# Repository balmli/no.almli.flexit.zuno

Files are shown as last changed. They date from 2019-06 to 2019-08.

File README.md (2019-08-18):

# Flexit SP 30

Flexit SP 30 panel to Z-UNO.

### Hardware

- [Z-UNO](https://products.z-wavealliance.org/products/1825)
- [SP425 controller board](https://www.flexit.no/produkter/ventilasjonsaggregat/utgatte_modeller/tilbehor_aggregater_utgatte_modeller/sp425_styringskort_for_sentralstyring_sd/styringskort_data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)
- 3 x 3 V relays
- 3 x 817 optocouplers
- 4 x DS18B20 temperature sensors 
- RJ45 wire
- breadboard
- resistors
- wires

### Build instructions:

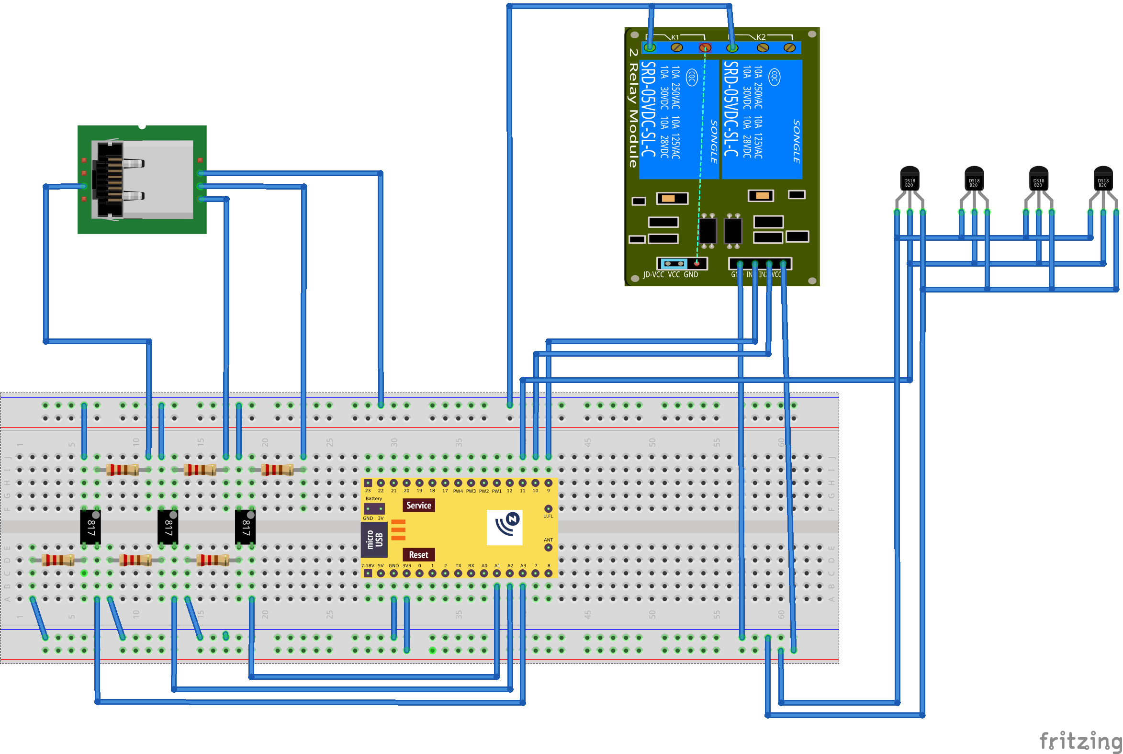
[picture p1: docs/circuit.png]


Connect the three 3 V relays to the Z-UNO:
- Z-UNO, pin  9: to relay 1 in
- Z-UNO, pin 10: to relay 2 in
- Z-UNO, pin 11: to relay 3 in
- 3V to relay Vin
- GND to relay GND-in

Connect the fan RJ45 wire to the breadboard:
- wire pin 3: to a diode, and then to relay 3 out
- wire pin 3: with a 1 kΩ resistor to optocoupler 3 input 
- wire pin 4: to relay 1,2,3 GND-out
- wire pin 5: to a 2.2 kΩ resistor, and then to relay 1 out
- wire pin 5: with a 1 kΩ resistor to optocoupler 1 input 
- wire pin 6: to a 2.2 kΩ resistor, and then to relay 2 out
- wire pin 6: with a 1 kΩ resistor to optocoupler 2 input 
- wire pin 7: to optocoupler 1,2,3 GND-in 

Connect the three optocouplers to the Z-UNO:
- optocoupler 1 out: to Z-UNO, pin A1
- optocoupler 2 out: to Z-UNO, pin A2
- optocoupler 3 out: to Z-UNO, pin A3
- optocoupler 1,2,3 GND-out: with 1 kΩ resistors to GND

Connect the four DS18B20 temperature sensors to the Z-UNO:
- Z-UNO, pin 12: to DS18B20 data pin
- 4.7 kΩ pullup resistor for DS18B20 data pin
- 5V to DS18B20 5V pins
- GND to DS18B20 GND pins

Connect power to the Z-UNO:
- Z-UNO, USB: power source
- Z-UNO, GND

### Firmware

Upload to Z-UNO by:

- install the Z-UNO software version 2.1.5 for Arduino.  See '[here](https://z-uno.z-wave.me/install)' for instructions.
- upload '[firmware](https://github.com/balmli/no.almli.flexit.zuno/blob/master/Flexit_SP30_ZUNO/Flexit_SP30_ZUNO.ino)'.

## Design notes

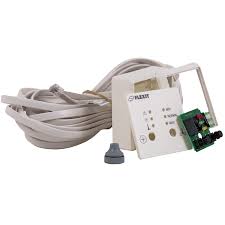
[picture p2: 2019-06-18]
docs/sp30.jpeg

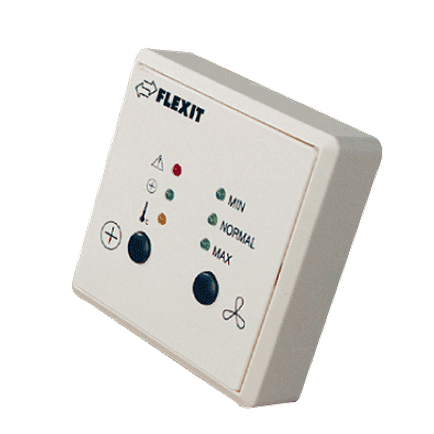
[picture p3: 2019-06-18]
docs/sp30.png

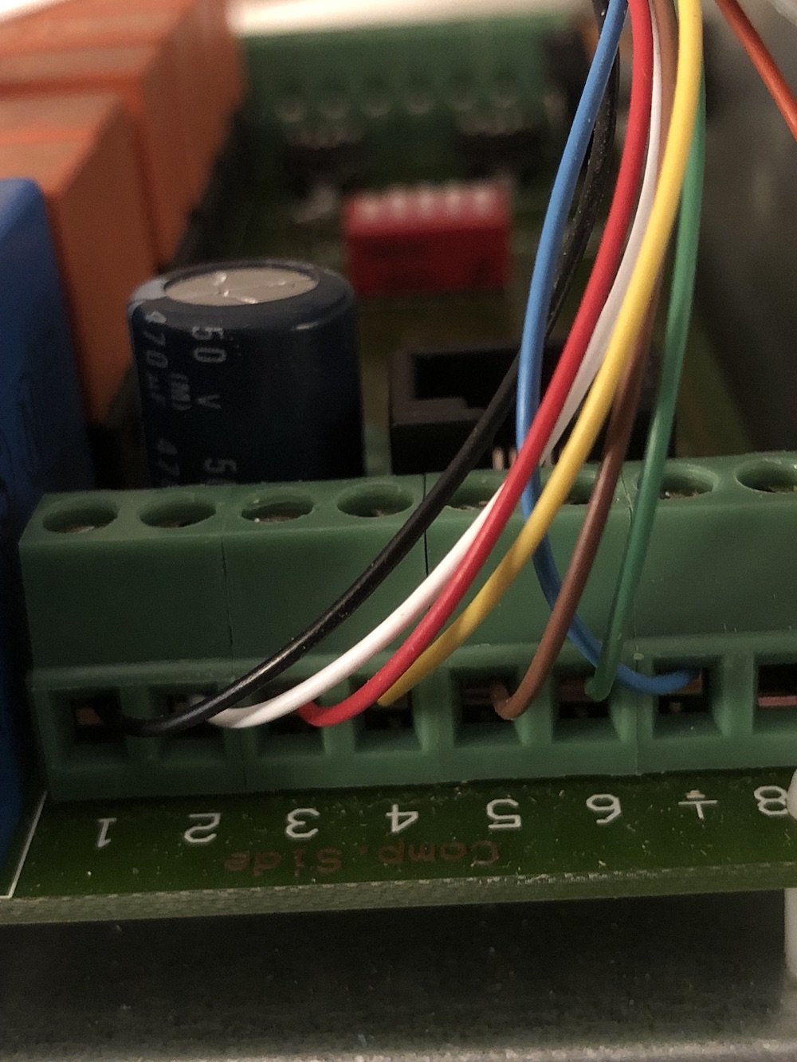
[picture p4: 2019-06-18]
docs/pins.jpg

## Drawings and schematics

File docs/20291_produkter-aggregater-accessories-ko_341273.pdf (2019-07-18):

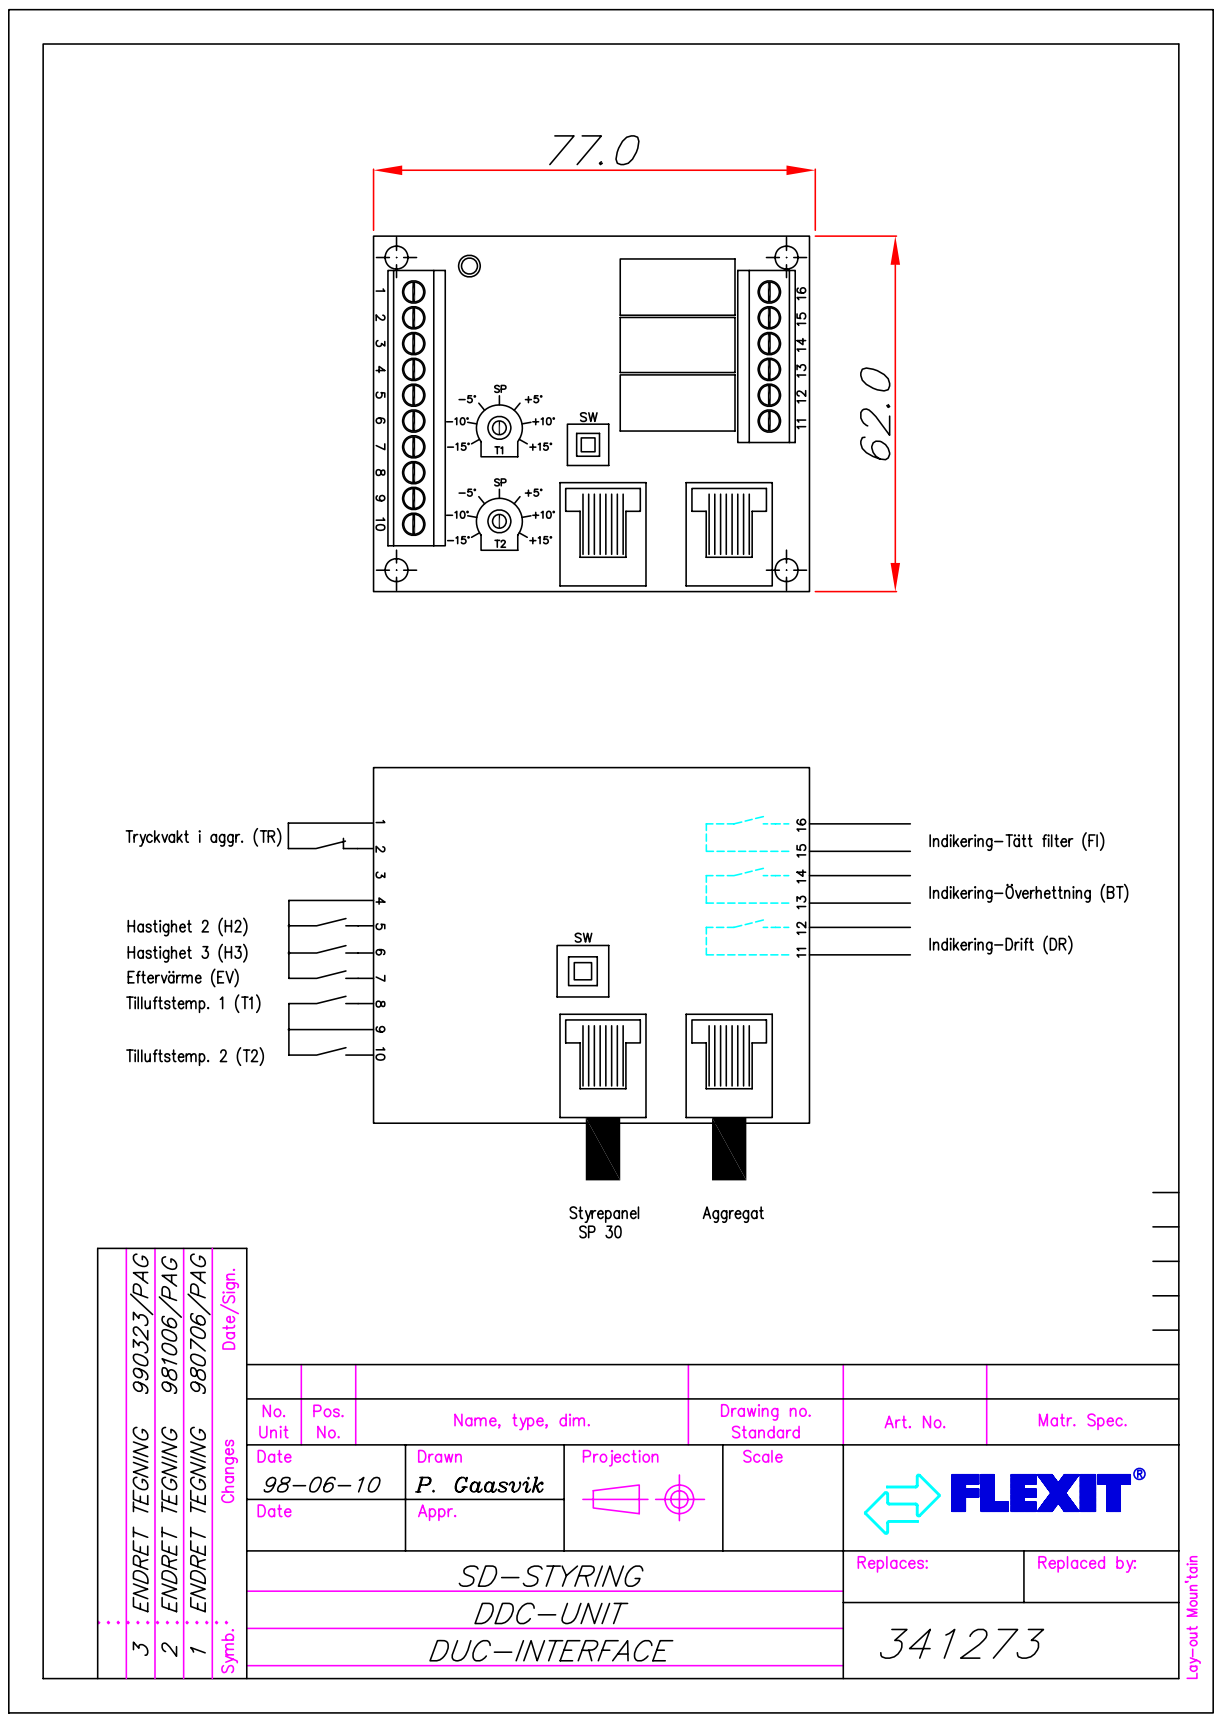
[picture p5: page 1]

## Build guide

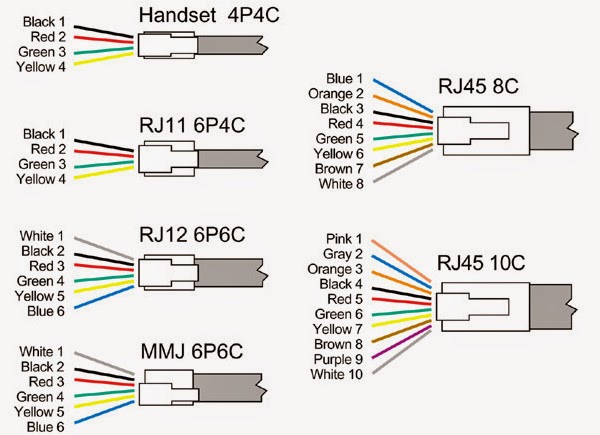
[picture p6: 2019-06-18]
docs/wiring_ms_modular_colour_codes_lg.jpg

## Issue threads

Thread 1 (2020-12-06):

Esphome variation

TomTorger, 2020-12-06:
Great work! Really helps me figuring this out :-)

I am considering doing this for with an esp32 and espHome for home assistant.

I am a bit in doubt as to the function of the relays... I am figuring they are similar to the "push-bottoms"? However, there are two/three 10 A relays in parallel according to your diagram? Could we use optocouplers here as well? (not a pro :-) )

Do you have a description of the pins 1-8 on the SP30 board? And does it supply a DC voltage above 5V somewhere?

Tom

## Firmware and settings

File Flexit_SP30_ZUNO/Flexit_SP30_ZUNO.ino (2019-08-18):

#include "ZUNO_DS18B20.h"
#include "EEPROM.h"

#define DEBUG_x

#define RELAY_1_PIN                 9
#define RELAY_2_PIN                 10
#define RELAY_3_PIN                 11
#define DS18B20_BUS_PIN             12
#define FAN_LEVEL_1_PIN             A1
#define FAN_LEVEL_2_PIN             A2
#define HEATING_PIN                 A3
#define LED_PIN                     LED_BUILTIN

#define MIN_UPDATE_DURATION         30000
#define MIN_STATE_UPDATE_DURATION   1000
#define MIN_TEMP_UPDATE_DURATION    30000
#define LED_BLINK_DURATION          25

OneWire ow(DS18B20_BUS_PIN);
DS18B20Sensor ds18b20(&ow);

#define MAX_TEMP_SENSORS            4
#define ADDR_SIZE                   8
byte addresses[ADDR_SIZE * MAX_TEMP_SENSORS];
#define ADDR(i) (&addresses[i * ADDR_SIZE])
byte temp_sensors;
word temperature[MAX_TEMP_SENSORS];
word temperatureReported[MAX_TEMP_SENSORS];
word temperatureCalibration[MAX_TEMP_SENSORS];

byte mode = 1;
byte modeChanged = 0;
unsigned long lastSetMode = 0;
byte lastFanLevel = 1;
byte lastFanLevelReported = 99;
byte lastHeating = 0;
byte lastHeatingReported = 99;

unsigned long relayTimer = 0;
unsigned long fanLevelTimer = 0;
unsigned long fanLevelTimer2 = 0;
unsigned long heatingTimer = 0;
unsigned long heatingTimer2 = 0;
unsigned long temperatureTimer[MAX_TEMP_SENSORS];
unsigned long ledTimer = 0;
unsigned long listConfigTimer = 0;

word status_report_interval_config;
word temperature_report_interval_config;
word temperature_report_threshold_config;
word relay_duration_config;
word enabled_config;
word enabled_mode_config;
word default_config_set_config;

ZUNO_SETUP_SLEEPING_MODE(ZUNO_SLEEPING_MODE_ALWAYS_AWAKE);
ZUNO_SETUP_PRODUCT_ID(0xC0, 0xC0);
ZUNO_SETUP_CFGPARAMETER_HANDLER(config_parameter_changed);

ZUNO_SETUP_CHANNELS(
    ZUNO_SWITCH_MULTILEVEL(getterMode, setterMode),

    ZUNO_SENSOR_MULTILEVEL(ZUNO_SENSOR_MULTILEVEL_TYPE_GENERAL_PURPOSE_VALUE,
        SENSOR_MULTILEVEL_SCALE_PERCENTAGE_VALUE,
        SENSOR_MULTILEVEL_SIZE_ONE_BYTE,
        SENSOR_MULTILEVEL_PRECISION_ZERO_DECIMALS,
        getterFanLevel),

    ZUNO_SENSOR_MULTILEVEL(ZUNO_SENSOR_MULTILEVEL_TYPE_GENERAL_PURPOSE_VALUE,
        SENSOR_MULTILEVEL_SCALE_PERCENTAGE_VALUE,
        SENSOR_MULTILEVEL_SIZE_ONE_BYTE,
        SENSOR_MULTILEVEL_PRECISION_ZERO_DECIMALS,
        getterHeating),

    ZUNO_SENSOR_MULTILEVEL(ZUNO_SENSOR_MULTILEVEL_TYPE_TEMPERATURE,
        SENSOR_MULTILEVEL_SCALE_CELSIUS,
        SENSOR_MULTILEVEL_SIZE_TWO_BYTES,
        SENSOR_MULTILEVEL_PRECISION_TWO_DECIMALS,
        getterTemp1),

    ZUNO_SENSOR_MULTILEVEL(ZUNO_SENSOR_MULTILEVEL_TYPE_TEMPERATURE,
        SENSOR_MULTILEVEL_SCALE_CELSIUS,
        SENSOR_MULTILEVEL_SIZE_TWO_BYTES,
        SENSOR_MULTILEVEL_PRECISION_TWO_DECIMALS,
        getterTemp2),

    ZUNO_SENSOR_MULTILEVEL(ZUNO_SENSOR_MULTILEVEL_TYPE_TEMPERATURE,
        SENSOR_MULTILEVEL_SCALE_CELSIUS,
        SENSOR_MULTILEVEL_SIZE_TWO_BYTES,
        SENSOR_MULTILEVEL_PRECISION_TWO_DECIMALS,
        getterTemp3),

    ZUNO_SENSOR_MULTILEVEL(ZUNO_SENSOR_MULTILEVEL_TYPE_TEMPERATURE,
        SENSOR_MULTILEVEL_SCALE_CELSIUS,
        SENSOR_MULTILEVEL_SIZE_TWO_BYTES,
        SENSOR_MULTILEVEL_PRECISION_TWO_DECIMALS,
        getterTemp4)
);

void setterMode(byte value) {
    mode = value;
    modeChanged = 1;
    lastSetMode = millis();
}

byte getterMode(void) {
    return mode;
}

byte getterFanLevel(void) {
  return lastFanLevel;
}

byte getterHeating(void) {
  return lastHeating;
}

word getterTemp1() {
    return temperature[0];
}

word getterTemp2() {
    return temperature[1];
}

word getterTemp3() {
    return temperature[2];
}

word getterTemp4() {
    return temperature[3];
}

void config_parameter_changed(byte param, word value) {
    if (param == 64) {
        status_report_interval_config = value;
    }
    if (param == 65) {
        temperature_report_interval_config = value;
    }
    if (param == 66) {
        temperature_report_threshold_config = value;
    }
    if (param == 67) {
        relay_duration_config = value;
    }
    if (param == 68) {
        enabled_config = value;
        if (enabled_config < 0 || enabled_config > 1) {
            enabled_config = 0;
        }
    }
    if (param == 69) {
        enabled_mode_config = value;
        if (enabled_mode_config < 0 || enabled_mode_config > 1) {
            enabled_mode_config = 0;
        }
    }
    if (param >= 70 && param <= 73) {
        temperatureCalibration[param - 70] = value;
    }

#ifdef DEBUG
    Serial.print("config ");
    Serial.print(param);
    Serial.print(" = ");
    Serial.println(value);
#endif
}

void setup() {
    pinMode(RELAY_1_PIN, OUTPUT);
    pinMode(RELAY_2_PIN, OUTPUT);
    pinMode(RELAY_3_PIN, OUTPUT);
    digitalWrite(RELAY_1_PIN, HIGH);
    digitalWrite(RELAY_2_PIN, HIGH);
    digitalWrite(RELAY_3_PIN, HIGH);
    pinMode(LED_PIN, OUTPUT);

    pinMode(FAN_LEVEL_1_PIN, INPUT_PULLUP);
    pinMode(FAN_LEVEL_2_PIN, INPUT_PULLUP);
    pinMode(HEATING_PIN, INPUT_PULLUP);

    Serial.begin();
    fetchConfig();
    temp_sensors = ds18b20.findAllSensors(addresses);
    fetchMode();
}

void fetchConfig() {
    status_report_interval_config = zunoLoadCFGParam(64);
    temperature_report_interval_config = zunoLoadCFGParam(65);
    temperature_report_threshold_config = zunoLoadCFGParam(66);
    relay_duration_config = zunoLoadCFGParam(67);
    enabled_config = zunoLoadCFGParam(68);
    enabled_mode_config = zunoLoadCFGParam(69);
    for (byte i = 0; i < MAX_TEMP_SENSORS; i++) {
        temperatureCalibration[i] = zunoLoadCFGParam(70 + i);
    }

    default_config_set_config = zunoLoadCFGParam(96);
    if (default_config_set_config != 1) {
        status_report_interval_config = 600;
        zunoSaveCFGParam(64, status_report_interval_config);

        temperature_report_interval_config = 600;
        zunoSaveCFGParam(65, temperature_report_interval_config);

        temperature_report_threshold_config = 20;
        zunoSaveCFGParam(66, temperature_report_threshold_config);

        relay_duration_config = 250;
        zunoSaveCFGParam(67, relay_duration_config);

        enabled_config = 0;
        zunoSaveCFGParam(68, enabled_config);

        enabled_mode_config = 0;
        zunoSaveCFGParam(69, enabled_mode_config);

        for (byte i = 0; i < MAX_TEMP_SENSORS; i++) {
            temperatureCalibration[i] = 0;
            zunoSaveCFGParam(70 + i, temperatureCalibration[i]);
        }

        default_config_set_config = 1;
        zunoSaveCFGParam(96, default_config_set_config);
    }
}

void fetchMode() {
    dword addr = 0x800;
    mode = EEPROM.read(addr);
    if (mode < 1 || mode > 13) {
        mode = 1;
    }
    modeChanged = 1;
    zunoSendReport(1);
}

void storeMode() {
    dword addr = 0x800;
    EEPROM.write(addr, mode);
}

void ledBlink(unsigned long timerNow) {
    ledTimer = timerNow;
    digitalWrite(LED_PIN, HIGH);
}

void ledBlinkOff(unsigned long timerNow) {
    if (ledTimer > 0 && (timerNow - ledTimer > LED_BLINK_DURATION)) {
        ledTimer = 0;
        digitalWrite(LED_PIN, LOW);
    }
}

void loop() {
    if (enabled_config == 1) {
        unsigned long timerNow = millis();
        if (enabled_mode_config == 1) {
            handleMode(timerNow);
        }
        getFanLevel(timerNow);
        getHeating(timerNow);
        reportFanLevel(timerNow);
        ledBlinkOff(timerNow);
        reportHeating(timerNow);
        ledBlinkOff(timerNow);
        reportTemperatures(timerNow);
        ledBlinkOff(timerNow);
#ifdef DEBUG
        listConfig(timerNow);
#endif
    }
}

void handleMode(unsigned long timerNow) {
    if ((modeChanged == 1) && ((timerNow - relayTimer) > relay_duration_config)) {
        relayTimer = timerNow;
        ledBlink(timerNow);

        byte r1 = ((mode % 10) == 2) ? LOW : HIGH;
        digitalWrite(RELAY_1_PIN, r1);

        byte r2 = ((mode % 10) == 3) ? LOW : HIGH;
        digitalWrite(RELAY_2_PIN, r2);

        byte r3 = ((mode - mode % 10) == 10) ? LOW : HIGH;
        digitalWrite(RELAY_3_PIN, r3);

        storeMode();
        modeChanged = 0;
        delay(25);

#ifdef DEBUG_3
        Serial.print(timerNow / 1000);
        Serial.print(": r1: ");
        Serial.print(r1);
        Serial.print(", r2: ");
        Serial.print(r2);
        Serial.print(", r3: ");
        Serial.println(r3);
#endif
    }
}

void getFanLevel(unsigned long timerNow) {
    int fl1 = digitalRead(FAN_LEVEL_1_PIN);
    int fl2 = digitalRead(FAN_LEVEL_2_PIN);
    lastFanLevel = fl1 == 1 && fl2 == 0 ? 3 : (fl1 == 0 && fl2 == 1 ? 2 : 1);

#ifdef DEBUG_2
    if (timerNow - fanLevelTimer2 > 2000) {
        fanLevelTimer2 = timerNow;
        Serial.print(timerNow / 1000);
        Serial.print(": fl1: ");
        Serial.print(fl1);
        Serial.print(", fl2: ");
        Serial.println(fl2);
        Serial.print(", fan level: ");
        Serial.print(lastFanLevel);
        Serial.print(", mode: ");
        Serial.println(mode);
    }
#endif
}

void getHeating(unsigned long timerNow) {
    int heat = digitalRead(HEATING_PIN);
    lastHeating = heat == 0 ? 10 : 0;

#ifdef DEBUG_2
    if (timerNow - heatingTimer2 > 2000) {
        heatingTimer2 = timerNow;
        Serial.print(timerNow / 1000);
        Serial.print(", heat: ");
        Serial.print(heat);
        Serial.print(", heating: ");
        Serial.print(lastHeating);
        Serial.print(", mode: ");
        Serial.println(mode);
    }
#endif
}

void reportFanLevel(unsigned long timerNow) {
    bool changed = lastFanLevel != lastFanLevelReported;
    unsigned long timer1Diff = timerNow - lastSetMode;
    unsigned long timer2Diff = timerNow - fanLevelTimer;
    unsigned long repInterval = ((unsigned long)status_report_interval_config) * 1000;

    if (changed && timer1Diff > MIN_STATE_UPDATE_DURATION || timer2Diff > repInterval) {
        lastFanLevelReported = lastFanLevel;
        fanLevelTimer = timerNow;
        ledBlink(timerNow);
        zunoSendReport(2);
#ifdef DEBUG_4
        Serial.print(timerNow / 1000);
        Serial.print(": lastFanLevel: ");
        Serial.println(lastFanLevel);
#endif
    }
}

void reportHeating(unsigned long timerNow) {
    bool changed = lastHeating != lastHeatingReported;
    unsigned long timer1Diff = timerNow - lastSetMode;
    unsigned long timer2Diff = timerNow - heatingTimer;
    unsigned long repInterval = ((unsigned long)status_report_interval_config) * 1000;

    if (changed && timer1Diff > MIN_STATE_UPDATE_DURATION || timer2Diff > repInterval) {
        lastHeatingReported = lastHeating;
        heatingTimer = timerNow;
        ledBlink(timerNow);
        zunoSendReport(3);
#ifdef DEBUG_4
        Serial.print(timerNow / 1000);
        Serial.print(": lastHeating: ");
        Serial.println(lastHeating);
#endif
    }
}

void reportTemperatures(unsigned long timerNow) {
    for (byte i = 0; i < temp_sensors && i < MAX_TEMP_SENSORS; i++) {

        unsigned long timerDiff = timerNow - temperatureTimer[i];
        unsigned long repInterval = ((unsigned long)temperature_report_interval_config) * 1000;

        if (timerDiff > MIN_TEMP_UPDATE_DURATION || timerDiff > repInterval) {

            temperature[i] = ((word)(ds18b20.getTemperature(ADDR(i)) * 100)) + temperatureCalibration[i];
            bool changed = temperature[i] > temperatureReported[i] + temperature_report_threshold_config || temperature[i] < temperatureReported[i] - temperature_report_threshold_config;

            if (changed && timerDiff > MIN_TEMP_UPDATE_DURATION || timerDiff > repInterval) {
                temperatureTimer[i] = timerNow;
                temperatureReported[i] = temperature[i];
                ledBlink(timerNow);
                zunoSendReport(i + 4);
#ifdef DEBUG_3
                Serial.print(timerNow / 1000);
                Serial.print(": temp[");
                Serial.print(i);
                Serial.print("]: ");
                Serial.println(temperature[i]);
#endif
            }
        }
    }
}

#ifdef DEBUG
void listConfig(unsigned long timerNow) {
    if (timerNow - listConfigTimer > MIN_UPDATE_DURATION) {
        listConfigTimer = timerNow;
        Serial.print("status_report_interval_config: ");
        Serial.println(status_report_interval_config);
        Serial.print("temperature_report_interval_config: ");
        Serial.println(temperature_report_interval_config);
        Serial.print("temperature_report_threshold_config: ");
        Serial.println(temperature_report_threshold_config);
        Serial.print("relay_duration_config: ");
        Serial.println(relay_duration_config);
        Serial.print("enabled_config: ");
        Serial.println(enabled_config);
        Serial.print("enabled_mode_config: ");
        Serial.println(enabled_mode_config);
        Serial.print("temp sensors: ");
        Serial.println(temp_sensors);
        for (byte i = 0; i < MAX_TEMP_SENSORS; i++) {
            Serial.print("temperatureCalibration[");
            Serial.print(i);
            Serial.print("]: ");
            Serial.println(temperatureCalibration[i]);
        }
    }
}
#endif

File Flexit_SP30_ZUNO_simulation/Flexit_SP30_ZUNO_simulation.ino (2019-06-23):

#include "ZUNO_DS18B20.h"

#define DEBUG
#define DEBUG_2
#define DEBUG_3

#define RELAY_1_PIN         9
#define RELAY_2_PIN         10
#define DS18B20_BUS_PIN     11
#define FAN_LEVEL_1_PIN     A1
#define FAN_LEVEL_2_PIN     A2
#define HEATING_PIN         A3
#define LED_PIN             LED_BUILTIN

#define RELAY_IN_1_PIN          18
#define RELAY_IN_2_PIN          17
#define FAN_LEVEL_OUT_1_PIN     PWM2
#define FAN_LEVEL_OUT_2_PIN     PWM3
#define HEATING_OUT_PIN         PWM4

#define MIN_UPDATE_DURATION     30000
#define LED_BLINK_DURATION      25

OneWire ow(DS18B20_BUS_PIN);
DS18B20Sensor ds18b20(&ow);

#define TEMP_SENSORS 4
#define ADDR_SIZE 8
byte addresses[ADDR_SIZE * TEMP_SENSORS];
#define ADDR(i) (&addresses[i * ADDR_SIZE])
byte number_of_sensors;
word temperature[TEMP_SENSORS];
word temperatureReported[TEMP_SENSORS];
word temperatureCalibration[TEMP_SENSORS];

byte switchValue = 1;
byte lastFanLevel = 1;
byte lastFanLevelReported = 1;
byte lastHeating = 0;
byte lastHeatingReported = 0;

byte sp30FanLevel = 1;
byte sp30Heating = 0;
byte prevSP30r1 = LOW;
byte prevSP30r2 = LOW;

unsigned long fanRelayOnTimer = 0;
unsigned long heatingRelayOnTimer = 0;
unsigned long relayTimer1 = 0;
unsigned long relayTimer2 = 0;
unsigned long fanLevelTimer = 0;
unsigned long fanLevelTimer2 = 0;
unsigned long heatingTimer = 0;
unsigned long heatingTimer2 = 0;
unsigned long temperatureTimer[TEMP_SENSORS];
unsigned long ledTimer = 0;
unsigned long listConfigTimer = 0;

word status_report_interval_config;
word temperature_report_interval_config;
word temperature_report_threshold_config;
word relay_duration_config;
word enabled_config;
word default_config_set_config;

ZUNO_SETUP_SLEEPING_MODE(ZUNO_SLEEPING_MODE_ALWAYS_AWAKE);
ZUNO_SETUP_PRODUCT_ID(0xC0, 0xC0);
ZUNO_SETUP_CFGPARAMETER_HANDLER(config_parameter_changed);

ZUNO_SETUP_CHANNELS(
    ZUNO_SWITCH_MULTILEVEL(getterSwitch, setterSwitch),

    ZUNO_SENSOR_MULTILEVEL(ZUNO_SENSOR_MULTILEVEL_TYPE_GENERAL_PURPOSE_VALUE,
        SENSOR_MULTILEVEL_SCALE_PERCENTAGE_VALUE,
        SENSOR_MULTILEVEL_SIZE_ONE_BYTE,
        SENSOR_MULTILEVEL_PRECISION_ZERO_DECIMALS,
        getterFanLevel),

    ZUNO_SENSOR_MULTILEVEL(ZUNO_SENSOR_MULTILEVEL_TYPE_GENERAL_PURPOSE_VALUE,
        SENSOR_MULTILEVEL_SCALE_PERCENTAGE_VALUE,
        SENSOR_MULTILEVEL_SIZE_ONE_BYTE,
        SENSOR_MULTILEVEL_PRECISION_ZERO_DECIMALS,
        getterHeating),

    ZUNO_SENSOR_MULTILEVEL(ZUNO_SENSOR_MULTILEVEL_TYPE_TEMPERATURE,
        SENSOR_MULTILEVEL_SCALE_CELSIUS,
        SENSOR_MULTILEVEL_SIZE_TWO_BYTES,
        SENSOR_MULTILEVEL_PRECISION_TWO_DECIMALS,
        getterTemp1),

    ZUNO_SENSOR_MULTILEVEL(ZUNO_SENSOR_MULTILEVEL_TYPE_TEMPERATURE,
        SENSOR_MULTILEVEL_SCALE_CELSIUS,
        SENSOR_MULTILEVEL_SIZE_TWO_BYTES,
        SENSOR_MULTILEVEL_PRECISION_TWO_DECIMALS,
        getterTemp2),

    ZUNO_SENSOR_MULTILEVEL(ZUNO_SENSOR_MULTILEVEL_TYPE_TEMPERATURE,
        SENSOR_MULTILEVEL_SCALE_CELSIUS,
        SENSOR_MULTILEVEL_SIZE_TWO_BYTES,
        SENSOR_MULTILEVEL_PRECISION_TWO_DECIMALS,
        getterTemp3),

    ZUNO_SENSOR_MULTILEVEL(ZUNO_SENSOR_MULTILEVEL_TYPE_TEMPERATURE,
        SENSOR_MULTILEVEL_SCALE_CELSIUS,
        SENSOR_MULTILEVEL_SIZE_TWO_BYTES,
        SENSOR_MULTILEVEL_PRECISION_TWO_DECIMALS,
        getterTemp4)
);

void setup() {
    Serial.begin();
    pinMode(RELAY_1_PIN, OUTPUT);
    pinMode(RELAY_2_PIN, OUTPUT);
    pinMode(LED_PIN, OUTPUT);

    pinMode(RELAY_IN_1_PIN, INPUT);
    pinMode(RELAY_IN_2_PIN, INPUT);
    pinMode(FAN_LEVEL_OUT_1_PIN, OUTPUT);
    pinMode(FAN_LEVEL_OUT_2_PIN, OUTPUT);
    pinMode(HEATING_OUT_PIN, OUTPUT);

    fetchConfig();
    number_of_sensors = ds18b20.findAllSensors(addresses);
}

void fetchConfig() {
    status_report_interval_config = zunoLoadCFGParam(64);
    temperature_report_interval_config = zunoLoadCFGParam(65);
    temperature_report_threshold_config = zunoLoadCFGParam(66);
    relay_duration_config = zunoLoadCFGParam(67);
    enabled_config = zunoLoadCFGParam(68);
    for (byte i = 0; i < TEMP_SENSORS; i++) {
        temperatureCalibration[i] = zunoLoadCFGParam(70 + i);
    }

    default_config_set_config = zunoLoadCFGParam(96);
    if (default_config_set_config != 1) {
        status_report_interval_config = 30;
        zunoSaveCFGParam(64, status_report_interval_config);

        temperature_report_interval_config = 300;
        zunoSaveCFGParam(65, temperature_report_interval_config);

        temperature_report_threshold_config = 2;
        zunoSaveCFGParam(66, temperature_report_threshold_config);

        relay_duration_config = 500;
        zunoSaveCFGParam(67, relay_duration_config);

        enabled_config = 0;
        zunoSaveCFGParam(68, enabled_config);

        for (byte i = 0; i < TEMP_SENSORS; i++) {
            temperatureCalibration[i] = 0;
            zunoSaveCFGParam(70 + i, temperatureCalibration[i]);
        }

        default_config_set_config = 1;
        zunoSaveCFGParam(96, default_config_set_config);
    }
}

void loop() {
    if (enabled_config == 1) {
        unsigned long timerNow = millis();
        handleSwitch(timerNow);
        checkFanLevel(timerNow);
        checkHeating(timerNow);
        checkTemperatures(timerNow);
        ledBlinkOff(timerNow);
        listConfig(timerNow);
    }
}

void config_parameter_changed(byte param, word value) {
#ifdef DEBUG
    Serial.print("config ");
    Serial.print(param);
    Serial.print(" = ");
    Serial.println(value);
#endif

    if (param == 64) {
        status_report_interval_config = value;
    }
    if (param == 65) {
        temperature_report_interval_config = value;
    }
    if (param == 66) {
        temperature_report_threshold_config = value;
    }
    if (param == 67) {
        relay_duration_config = value;
    }
    if (param == 68) {
        enabled_config = value;
        if (enabled_config < 0 || enabled_config > 1) {
            enabled_config = 0;
        }
    }
    if (param >= 70 && param >= 73) {
        temperatureCalibration[param - 70] = value;
    }
}

void listConfig(unsigned long timerNow) {
#ifdef DEBUG
    if (timerNow - listConfigTimer > MIN_UPDATE_DURATION) {
        listConfigTimer = timerNow;
        Serial.print("status_report_interval_config: ");
        Serial.println(status_report_interval_config);
        Serial.print("temperature_report_interval_config: ");
        Serial.println(temperature_report_interval_config);
        Serial.print("temperature_report_threshold_config: ");
        Serial.println(temperature_report_threshold_config);
        Serial.print("relay_duration_config: ");
        Serial.println(relay_duration_config);
        Serial.print("enabled_config: ");
        Serial.println(enabled_config);
        for (byte i = 0; i < TEMP_SENSORS; i++) {
            Serial.print("temperatureCalibration[");
            Serial.print(i);
            Serial.print("]: ");
            Serial.println(temperatureCalibration[i]);
        }
    }
#endif
}
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

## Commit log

2019-06-23 - temperature change reporting, if outside threshold and within min-update-duration or if after the temp-report-interval - default temp-report-interval is 300 seconds
2019-07-07 levels -> just for testing fan levels and heating from the SP30 panel
    simulation -> simulates the state of the SP30 panel
2019-07-07 Arduino UNO for testing the optocouplers
2019-07-07 levels -> just for testing fan levels and heating from the SP30 panel
2019-07-08 enable / disable relay switching
2019-07-08 fix status and temp reporting
    [Flexit_SP30_ZUNO.ino]
2019-07-09 try to fix status and temp reporting
    [Flexit_SP30_ZUNO.ino]
2019-07-18 - store mode in EEPROM - fetch mode from EEPROM on power up - report mode, fan level and heating on power up - report mode on changes from the SP30 panel
2019-07-19 relay off, not on, when powering on
2019-08-18 do not report changes to fan level or heating to channel 1
